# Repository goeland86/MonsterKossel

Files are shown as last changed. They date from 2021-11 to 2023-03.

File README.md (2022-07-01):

# Monster Kossel: v3.0

A Kossel-inspired Delta printer with:
* large build volume
* an incredibly stiff frame
* an easily fully enclosed build volume
* piezo-based bed probing (Andromeda layout from precisionpiezo.co.uk)
* easy to tune / upgrade setups
* M3 and M5 screws only

The image is missing the second rod per tower, and is not showing some of the screws - this is normal. A photo of the final, assembled printer is coming.
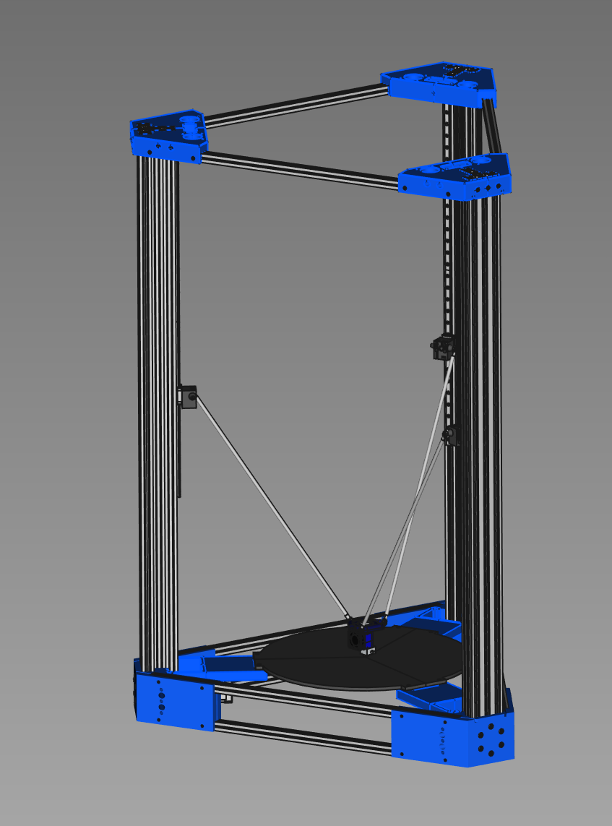
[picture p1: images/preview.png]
Monster Kossel


## Design history:

V1 started with my taking a Kossel XL idea but noticing the OpenBeam frames just weren't rigid enough. 
I tweaked the STL files with Blender to use 2040 towers instead. It was better... But still a bit wobbly.

V2 was still done with Blender but introduced the T-based towers using 2060 and 2040 extrusions for the maximum possible rigidity.
It also introduced the concept of the fully enclosed build volume. 

It became the test bed for a series of remote drive extruder designs by Dan Cook, which are proving to be incredibly reliable.
The latest iteration of which is a mix of extruder and effector design for Kossel sized rod widths. 
It's proven to handle flexibles as good as a Prusa MK3's stock extruder, if not better.

V3, shared here, is an ongoing effort to properly draw and design a revision of V2 in a proper CAD format.
The aim is to further enhance the experience by incorporating many lessons learned with regards to cable management.
It is currently being drawn and assembled in FreeCAD 0.19_pre release, using the Assembly4 plugin.

## Assembly file(s)

The main assembly file is `MonsterKossel_assembly.FCStd`, made for the `Assembly3` workbench that you can find from the addon manager, use with FreeCAD 0.20+.

The other workbench that is required is the `Fasteners` workbench, to include all the screws & nuts into the assembly.

## Current development status

The main frame of V3 has not yet been fully tested in real life, and the CAD design is undergoing multiple improvements as the tests continue. However at this stage the mechanics are considered solid and the dimensions will not change significantly.
Any further improvements will be to improve assembly, printability or esthetics.

Dan Cook has released his all in one effector / direct drive extruder on [Thingiverse](https://www.thingiverse.com/thing:4886240/files), including the telescoping shaft of my conception.

Carriages have been redrawn as the original Kossel carriages designed for the MGN19H carriage pattern don't have enough rigidity when using an adapter plate.

All parts will are printed in PETG rather than PLA for heat resistance. ABS, PCTG, PC are all possible options for the printed parts to be used. Avoid Nylons and other more flexible materials, as the parts need to be as rigid as possible to maintain dimensional stability of the assembled printer.

The top cover will come in two versions: one as a blank template for builders to customize the layout of elements on their own, the other as I intend to build it, using 100mm (a little under 4" diameter, standard in Europe) AC extraction ventilation systems with filters, wiring and filament paths etc.

### BOM

#### Printed parts:

Best rigidity achieved using PETG or similar flexibility of material, with 1 or 1.2mm thick walls, and 20% infill, and 0.2 or 0.3 layer height. Avoid PLA at least for the motor frames to avoid heat-induced deformation over time.

- bottom corner: 3x

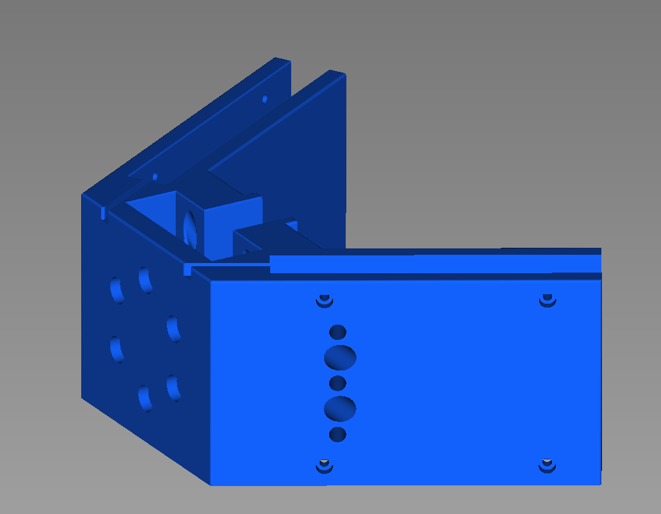
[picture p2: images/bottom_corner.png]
Bottom corner


- motor frame: 3x (print upside down, flip 180 degrees along x or y in your slicer)

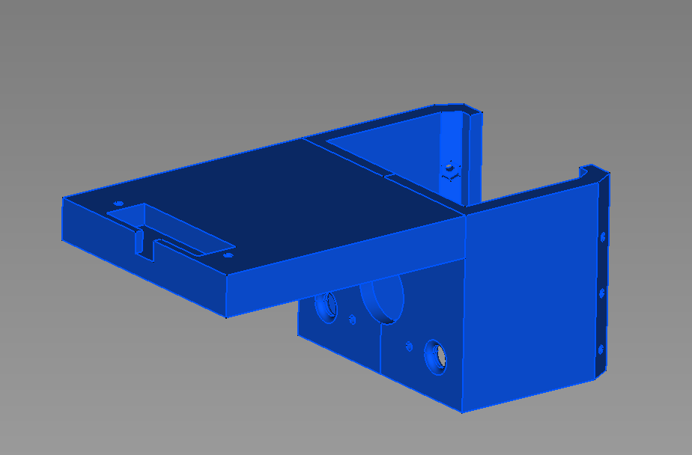
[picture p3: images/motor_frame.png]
Motor frame


- top corner: 3x

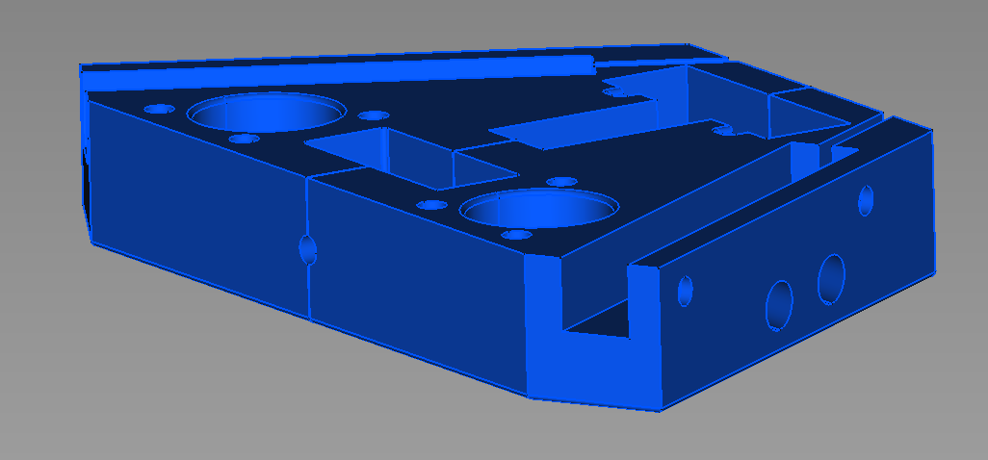
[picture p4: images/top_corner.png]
Top corner


- carriage belt tensioner: 3x

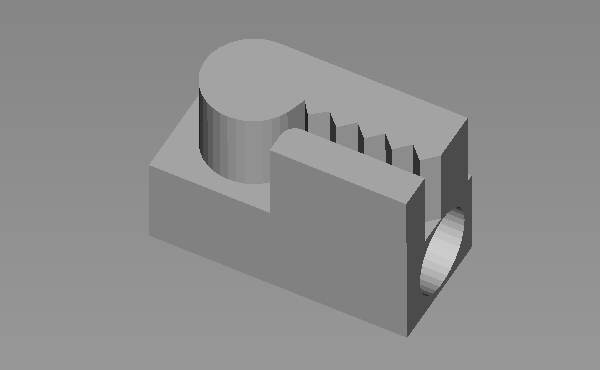
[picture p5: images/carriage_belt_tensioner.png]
carriage belt tensioner


- mgn9c carriage: 3x

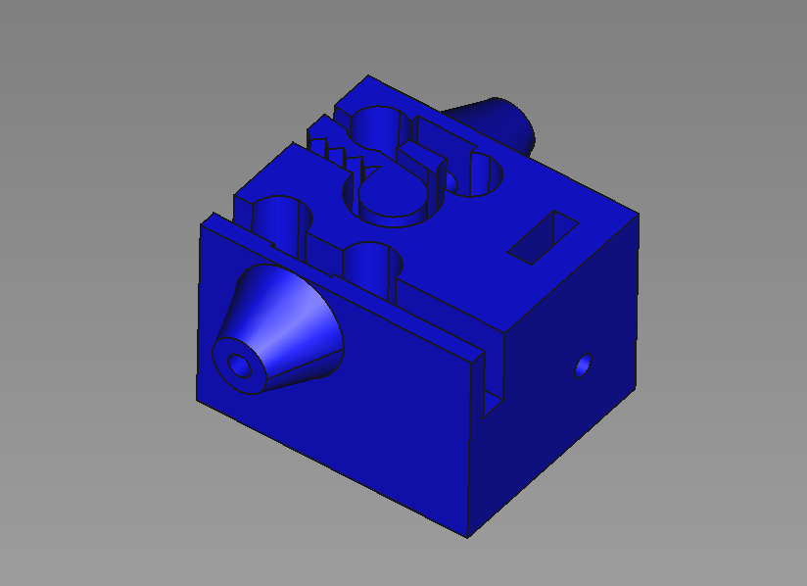
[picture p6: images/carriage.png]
carriage


- extruder parts (all are x1, printed with finer layer height is better):
  - 18T bevel
  - 6T bevel
  - Body top
  - Delta effector
  - Latch
  - Main body center
  - Main body left
  - Main body right

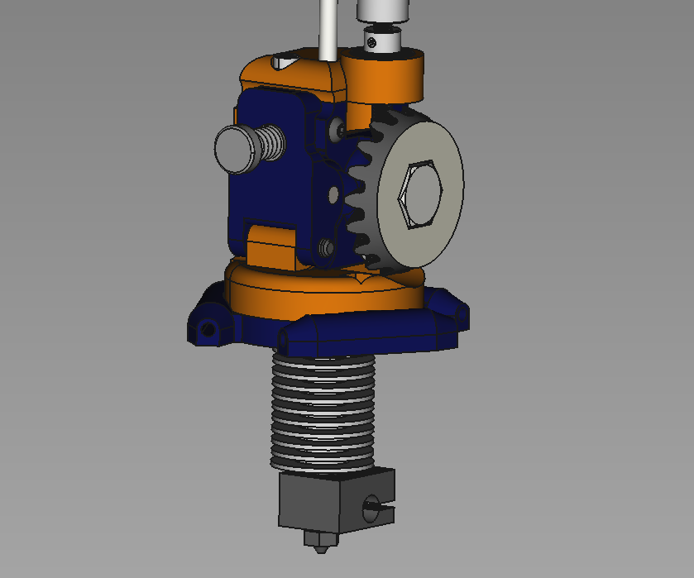
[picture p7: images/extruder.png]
extruder


OPTIONAL 

- base corner holder 6x (recommend in flexible material to dampen vibrations, to hold the printer properly in place on a plate/table).

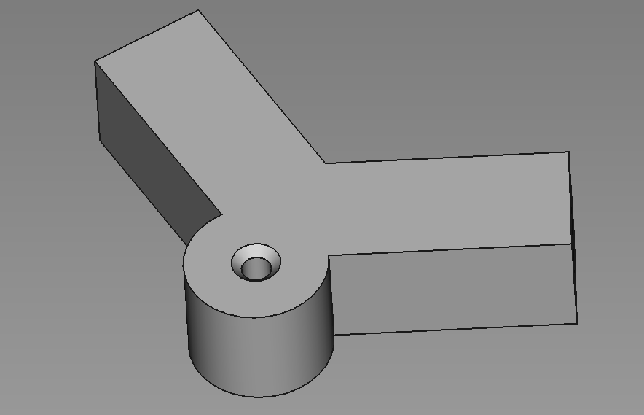
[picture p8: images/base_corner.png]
base corner


- CPAP-fan-diffuser 1x (to bring in part cooling air from an outside fan blowing cold air onto the part, recommend PETG/high temp material)

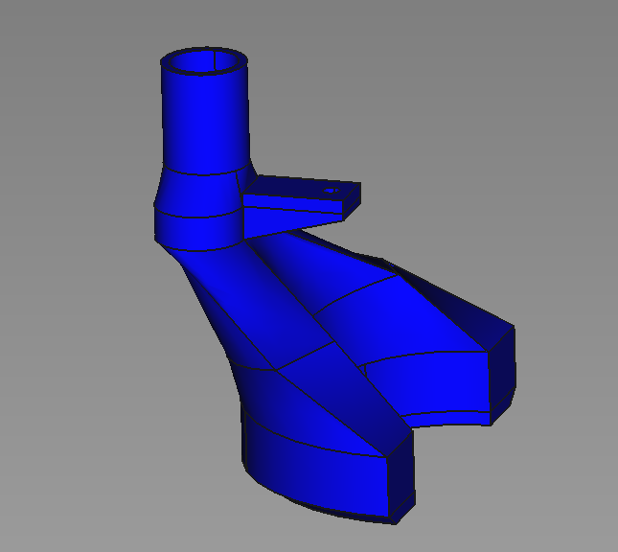
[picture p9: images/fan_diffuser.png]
fan diffuser


If using an E3D watercooling kit for the hotend:

- Watercooling-pump-bracket-bottom x1

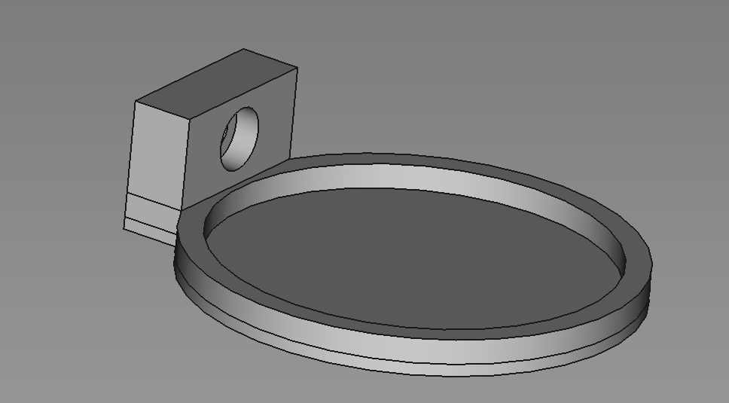
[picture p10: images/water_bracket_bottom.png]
watercooling bracket bottom


- Watercooling-pump-bracket-top x1

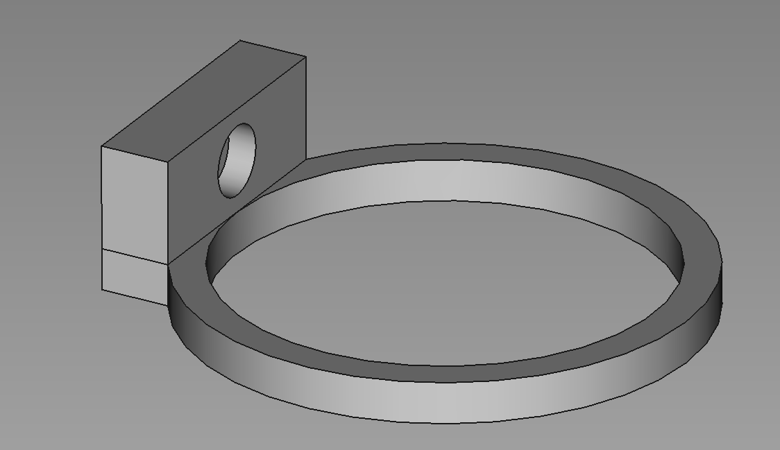
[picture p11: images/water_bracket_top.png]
watercooling bracket top


- bearing ujoint cube x2

- bearing ujoint fitting x4

#### Non-printed parts:

- Power supply (count about 40 to 50W for the motors, plus what your hotend, electronics and fans use)
- Electronics controller (32bit controller highly recommended, numerical precision requires extra computational power). I run mine with a [Recore](https://www.iagent.no/product/recore/)
- MGN9H rails: 3
- MGN9C carriages: 3
- NEMA17 motors: 4
- Traxxas 5347 spherical joints: 12
- carbon / aluminum rods: estimate 6x 390mm for a 350mm bed - identical lengths required (< 0.1mm difference in lengths recommended)
- E3D V6 hotend with M-12 threaded heatsink ([blue heatsink](https://e3d-online.com/products/v6-threaded-heatsink)): 1 (if enclosed, consider getting a [water-cooled, M12-mounting](https://www.thingiverse.com/thing:3088118/files) heatsink or hotend instead)
- Telescoping torque shaft:
 - aluminum square tubing 9mm on the side : length to be measured
 - aluminum square tubing 12mm on the side : length to be measured
 - aluminum square tubing 15mm on the side : length to be measured
 - double u-joints with 4mm shaft: 2
 - round 4mm steel rod: 2x 50mm
- [PrecisionPiezo Andromeda](https://www.precisionpiezo.co.uk/product-page/andromeda) : 3
- [PrecisionPiezo Universal Piezo Z-Probe PCB](https://www.precisionpiezo.co.uk/product-page/universal-piezo-z-probe-pcb-v2-x-for-1-2-3-or-more-piezos) : 1
- Endstops: 3 (optional if your electronics & firmware supports high precision sensorless homing)
- Electrical wiring (red and black recommended in equal lengths): ~ 10m of each color recommended. Lots of variability depending on placements.
- GT2-6mm wide belt: 3 times twice the vertical extrusion length (for 1m tall, get 3 of 2m length, will give ~100mm of slack per tower)
- Control board: minimum of 4 stepper drivers + 2 heater controls (2 temperature inputs, 2 MOSFETs)
- PSU: Minimum of 650W if heatbed is not using AC and a relay
- M3 nuts: 69 (bottom assembly: 42, top frame: 12, motor frames: 9, idler centering: 6)
- M3 washers: 18 (motor frames: 18)
- socket cap M3x5: 15 (motor frames: 3, carriage assemblies: 12)
- socket cap M3x8: 69 (tower assemblies: 45, top frame: 12, motor frames: 12)
- socket cap M3x10: 24 (bottom frame: 24)
- button cap M3x15 : 6 (motor frames: 6) - can also be longer, for bed assembly, but no longer than M3x30 (blocked by the NEMA 17 motor otherwise)
- socket cap M3x16: 18 (bottom frame assembly: 18) - can also be M3x15
- countersunk head M3x20: 6 (bottom frame assembly: 6)
- socket cap M3x30: 3
- socket cap M5x8: 24 (top frame: 12, bottom frame: 12)
- socket cap M5x10: 9 (top frame: 9)
- socket cap M5x12: 18 (bottom frame: 18)
- socket cap M5 Openbuilds flat nuts: 51
- F623ZZ flanged bearings: 6 OR idler pulleys for GT2x6mm : 3
- Nema 17 motors (1.8 degree is fine, 1.2-1.5A capability sufficient): 4
- 16-teeth pulley for 5mm shaft (with M3x4 set screw): 3
- Acrylic/glass/wood sheet (3mm): 3x 810mm x 500mm (use dimensions of side_panel file instead)
- Acrylic/wood/carbon/fiberglass sheet (5mm): 450mm x 400mm (cut using top_cover dimensions)
- Extruder parts:
  - M8x35 bolt: 1
  - MR 148ZZ bearings (8mm ID, 14mm OD, 4mm thick): 4
  - Bondtech [dual drive gears 1.75 / 8](https://www.bondtech.se/product/drivegear-kits/): 1 set
  - M3x12 hex socket cap
  - M4x40 set screw
  - M3x8 hex socket cap
- MR 84 ZZ bearings (ID 4mm, OD 8 mm, 3mm thick) x4
- Needle bearings (ID 4mm, OD 7mm, length 7mm) x4

##### Optional parts

- [CPAP fan + driver](https://www.aliexpress.com/item/33041228096.html?spm=a2g0o.9042311.0.0.38a54c4dUW6Yg9)
- CPAP mounting plate printed 1x
- [E3D watercooling kit](https://e3d-online.com/products/water-cooling-kit)
- Printed M12 nut 1x (make it 100% infill for robustness)

## Credit

I want to thank [Dan Cook](https://www.thingiverse.com/dancook3d/designs) for his wonderful [bevel geared extruder design](https://www.thingiverse.com/thing:4886240/files). We've exchanged a fair bit to iterate the design before he published it, and I'm happy to see that project being this successful on its own.

Additionally he made a [great delta carriage](https://www.thingiverse.com/thing:3070352) which I'm using the tensioner design from in this project.
Both of those designs you'll find the relevant step files in the `STEP` subfolder, and they're straight copies from his Thingiverse designs. I just included them for completeness here.

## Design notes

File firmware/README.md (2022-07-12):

### Monster Kossel: the firmware

At time of writing, the Monster Kossel has never been run with Marlin.

There's no reason it can't. A good SKR board and some finagling with Marlin will get you there for sure.

However I have been a long-time fan and contributor to the [Intelligent-Agent](https://github.com/intelligent-agent/) series of boards for the firmware.

Versions 1 and 2 of the Monster Kossel have run on the original Replicape + Beaglebone Black combo. Then when it was made available to me for beta testing, I switched it over to a Recore.
This means that I've only run two firmwares on this delta: Redeem (abandoned firmware for the Replicape), and Klipper.

Because I have never tried (nor wanted to) run it on any other board, I can only provide my Klipper configuration file for Recore for my delta.

# WARNING!

If you do not use Recore, the klipper config may be deprecated. That is because Recore is currently running its own fork of Klipper.
While it was developed specifically for Klipper usage, some new chip supports were needed in the base code, and as far as I know this hasn't yet merged upstream.

If you're using Recore and are building a 350mm bed, with 1000mm tall extrusions, this should be nearly plug & play. Simply make sure to re-measure your delta rod lengths and re-run the calibration routine.

Obviously if you're diverging from the BOM listed for the design, you'll need to adjust the config accordingly.

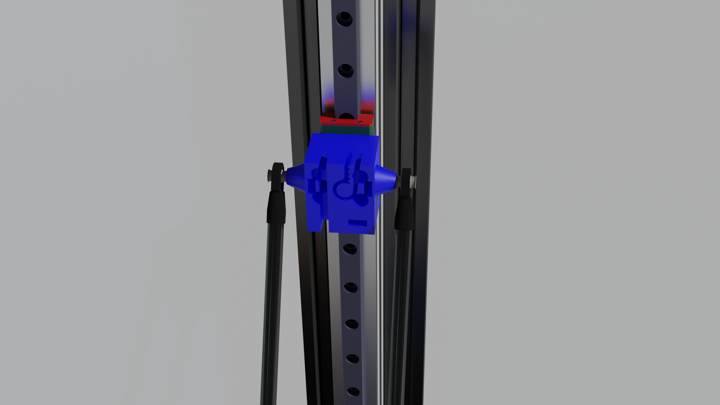
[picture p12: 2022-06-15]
images/carriage_detail.png

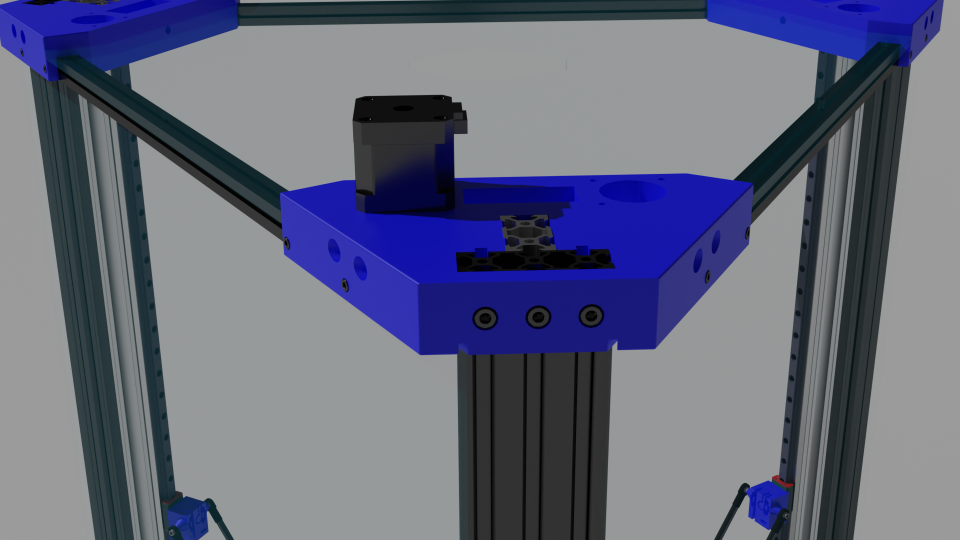
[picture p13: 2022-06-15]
images/Top_corner_motor_zoom.png

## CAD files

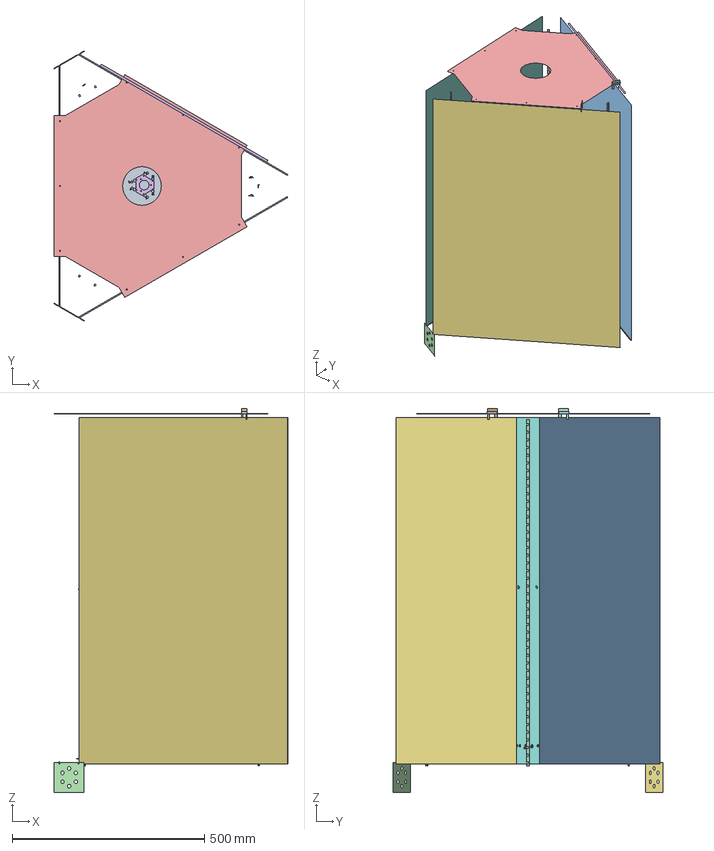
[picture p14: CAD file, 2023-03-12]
Assembly.FCStd
608.1 x 701.3 x 998.5 mm
_Element
_Element001
_Element002
_Element003
_Element004
_Element005
_Element006
_Element007
_Element008
_Element009
_Element010
_Element011
_Element012
_Element013
_Element014
_Element015
_Element016
_Element017
_Element018
_Element019
_Element020
_Element021
_Element022
_Element023
_Element024
_Element025
_Element026
_Element027
_Element028
_Element029
_Element030
_Element031
_Element032
_Element033
_Element034
_Element035
_Element036
_Element037
_Element038
_Element039
_Element040
_Element041
_Element042
_Element043
_Element044
_Element045
_Element046
_Element047
_Element048
_Element049
_Element052
_Element053
_Element054
_Element055
_Element057
_Element058
_Element059
_Element060
_Element061
_Element063

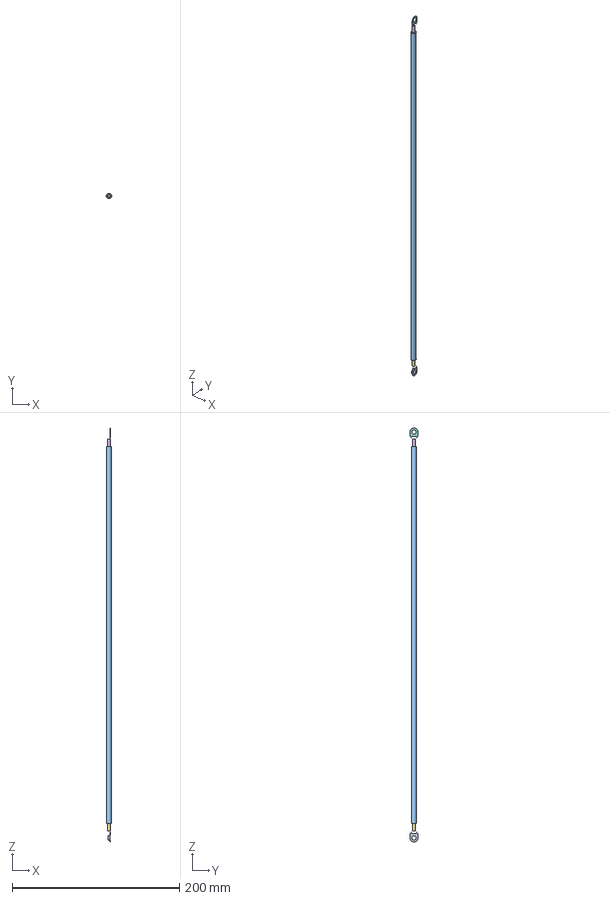
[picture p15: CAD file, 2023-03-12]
rod_assembly.FCStd
6.60 x 9.70 x 494.4 mm
Element
_Element
_Element002
_Element004
_Element006
_Element007
_Element008
_Element009
_Element010
_Element011
_Element012

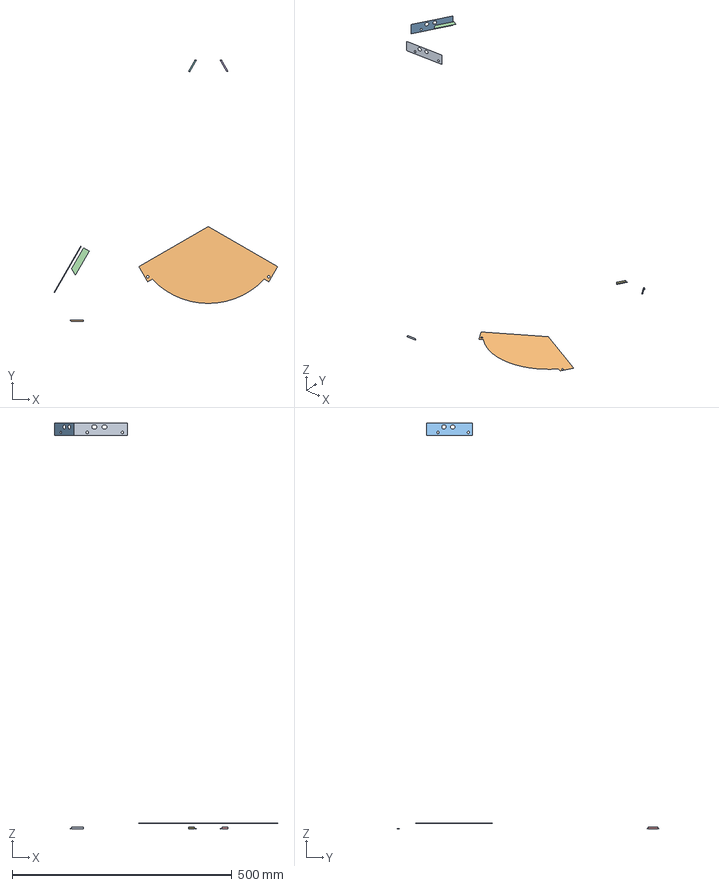
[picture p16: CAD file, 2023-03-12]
Complete_printer.FCStd
508.2 x 607.0 x 923.9 mm
_Element001
_Element002
_Element004
_Element006
_Element008
_Element010
_Element014
_Element016
_Element020
_Element022

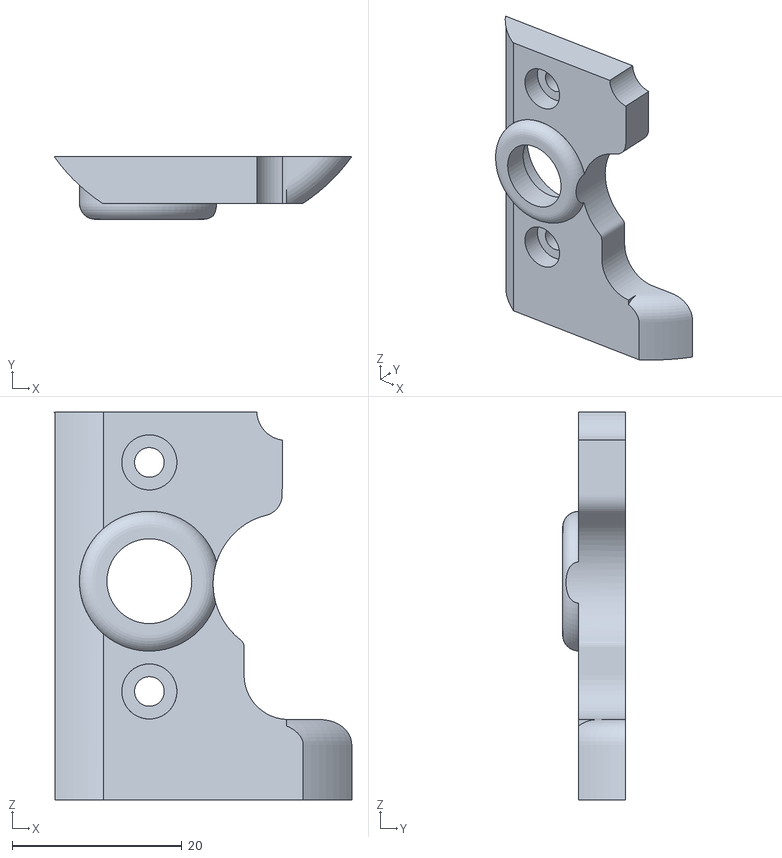
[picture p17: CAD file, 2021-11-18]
STL/effector-extruder-files/Main_Body_Right.stl
35.1 x 7.40 x 45.7

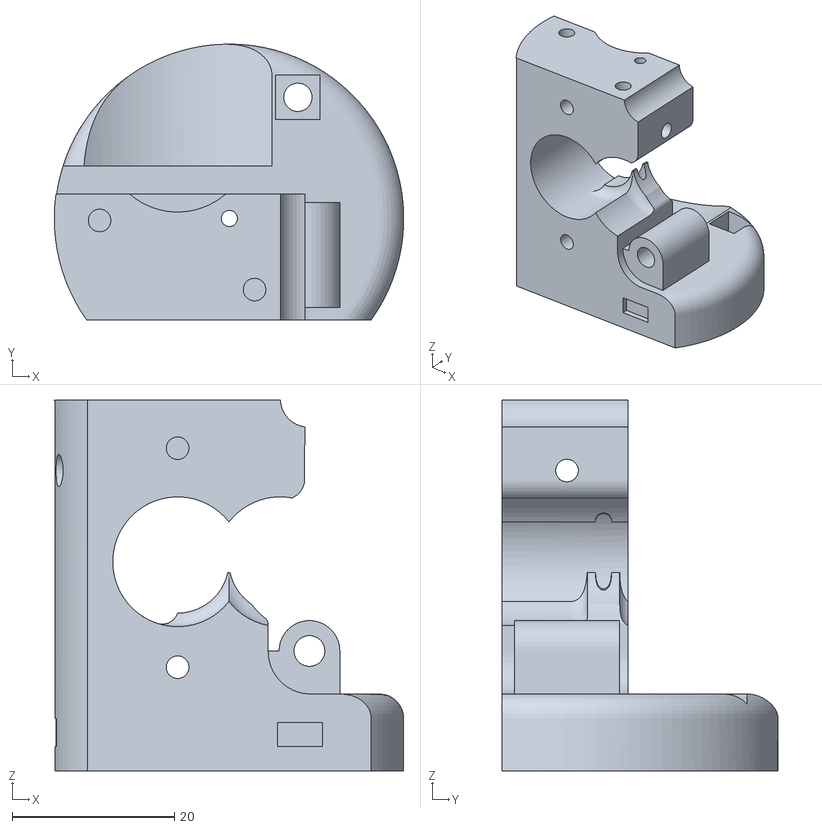
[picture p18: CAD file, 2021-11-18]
STL/effector-extruder-files/Main_Body_Center.stl
43.1 x 34.0 x 45.7

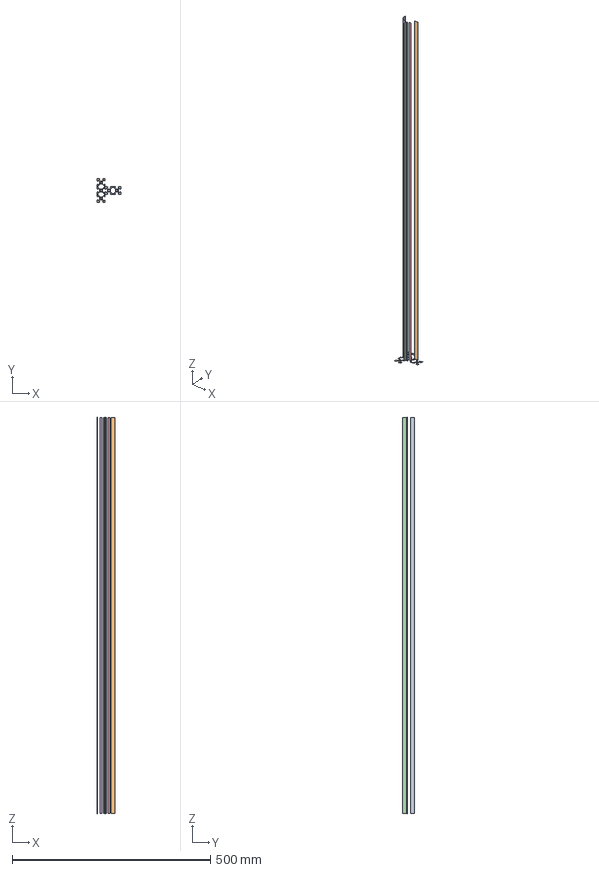
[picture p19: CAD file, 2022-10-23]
Vertical_extrusion_assembly.FCStd
60.0 x 60.0 x 1000.0 mm
Element
Element001
_Element
_Element001
_Element002
_Element003
_Element004
_Element005
_Element006
_Element007

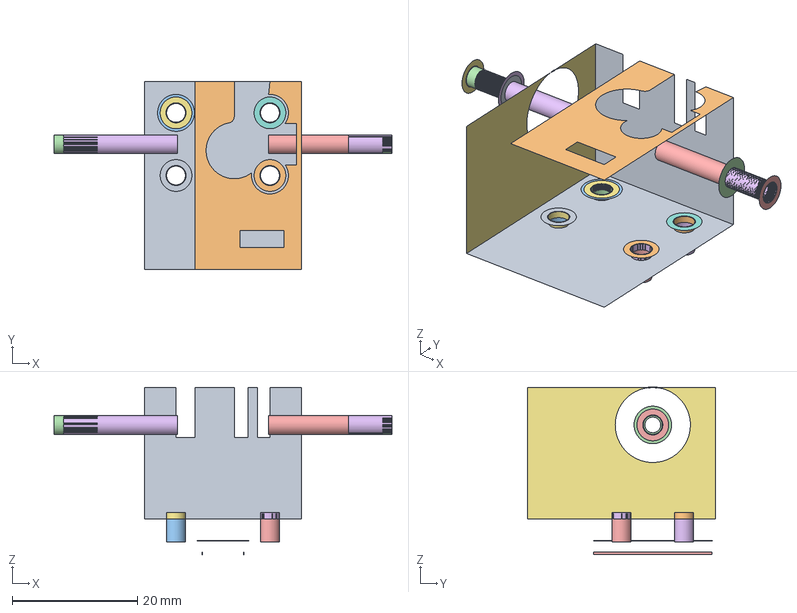
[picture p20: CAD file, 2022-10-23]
carriage_assembly.FCStd
54.0 x 30.0 x 26.7 mm
Element
Element001
Element002
Element003
Element004
Element005
Element006
Element007
Element012
_Element
_Element008
_Element010
_Element011
_Element012
_Element015
_Element016
_Element017
_Element018
_Element019
_Element020
_Element021
_Element022
_Element023
_Element024
_Element025
_Element026
_Element027
_Element032
_Element033
_Element035
_Element036
_Element037
_Element038
_Element039
_Element040
_Element041
_Element042
_Element043

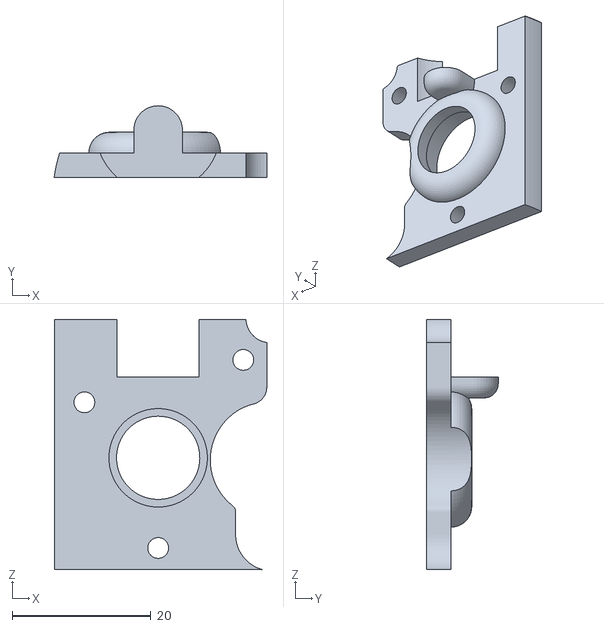
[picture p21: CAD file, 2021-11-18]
STL/effector-extruder-files/Main_Body_Left.stl
30.7 x 10.3 x 36.0

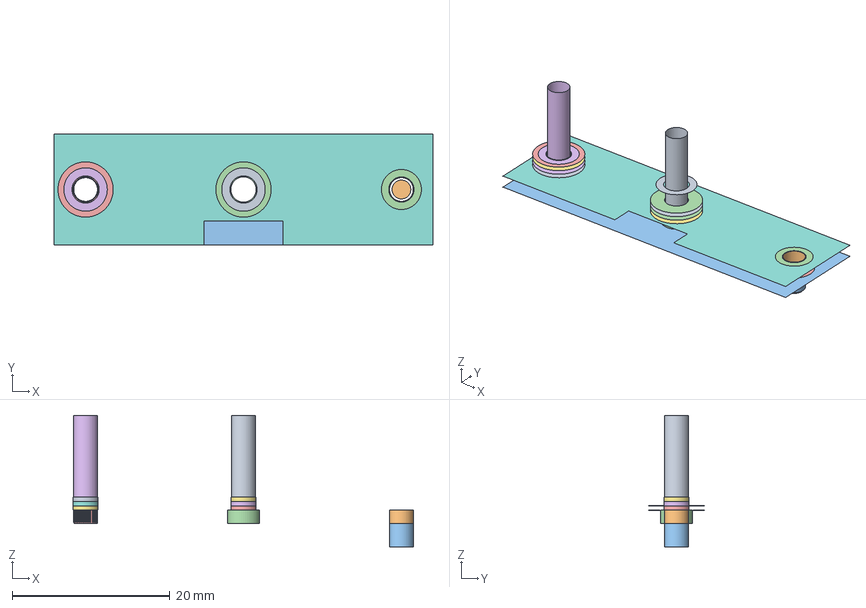
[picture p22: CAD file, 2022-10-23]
piezo_assembly.FCStd
48.0 x 14.0 x 17.0 mm
Element
Element002
_Element
_Element001
_Element002
_Element003
_Element004
_Element005
_Element006
_Element007
_Element008
_Element009
_Element010
_Element011
_Element012
_Element013
_Element014
_Element015
_Element016
_Element017
_Element018
_Element019
_Element020
_Element021
_Element022
_Element023
_Element024
_Element025
_Element026
_Element027
_Element028
_Element029
_Element030
_Element031
_Element032
_Element033
_Element034

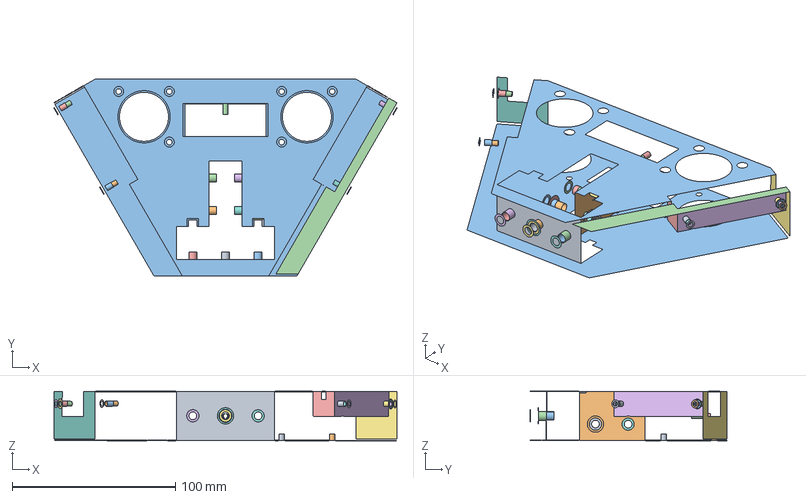
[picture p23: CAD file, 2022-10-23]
top_corner_assembly.FCStd
210.1 x 120.5 x 30.3 mm
Element
Element001
Element002
Element003
Element004
Element005
Element006
Element007
Element008
Element009
_Element
_Element001
_Element002
_Element003
_Element004
_Element005
_Element006
_Element007
_Element008
_Element009
_Element010
_Element011
_Element012
_Element013
_Element014
_Element015
_Element016
_Element017
_Element018
_Element019
_Element020
_Element021
_Element022
_Element023
_Element024
_Element025
_Element026
_Element027
_Element028
_Element029
_Element030
_Element031
_Element032
_Element033
_Element034
_Element035
_Element037
_Element038
_Element039
_Element041
_Element042
_Element043
_Element045

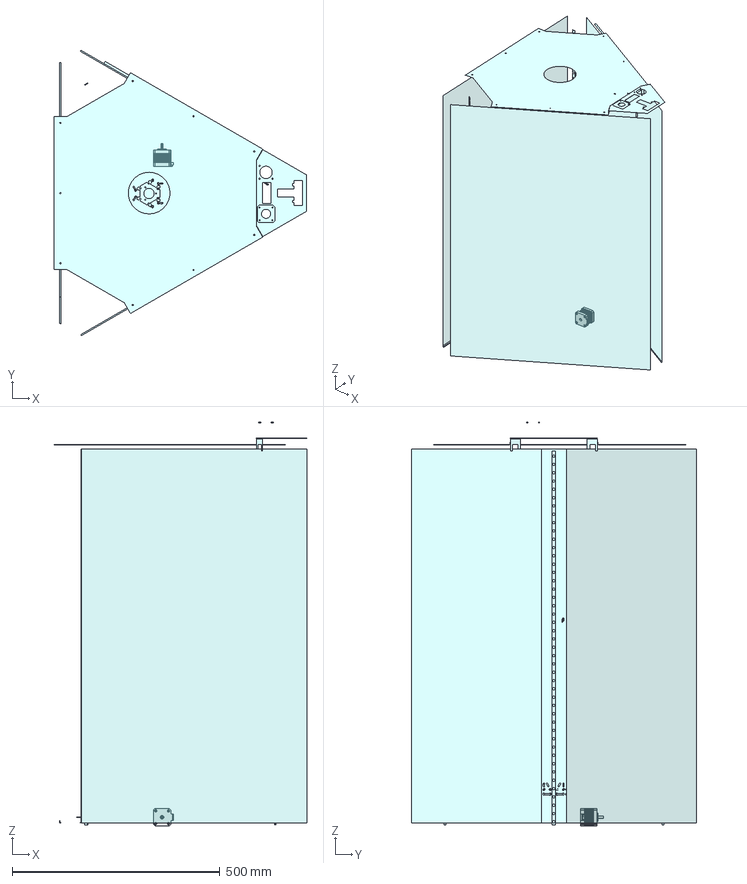
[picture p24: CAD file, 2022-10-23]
Assembly-for-render.FCStd
607.9 x 686.7 x 972.0 mm
_Element
_Element001
_Element002
_Element003
_Element004
_Element005
_Element006
_Element007
_Element008
_Element009
_Element010
_Element011
_Element012
_Element037
_Element038
_Element040
_Element041
_Element042
_Element043
_Element044
_Element045
_Element046
_Element048
_Element052
_Element054
_Element058
_Element059
_Element060
_Element061
_Element081
_Element085
_Element086
_Element088
_Element092
_Element095
_Element098
_Element100
_Element110
_Element112
_Element114
_Element115
_Element123
_Element124
_Element125
_Element126
_Element127
_Element128
_Element129
_Element130
_Element131
_Element132
_Element133
_Element134

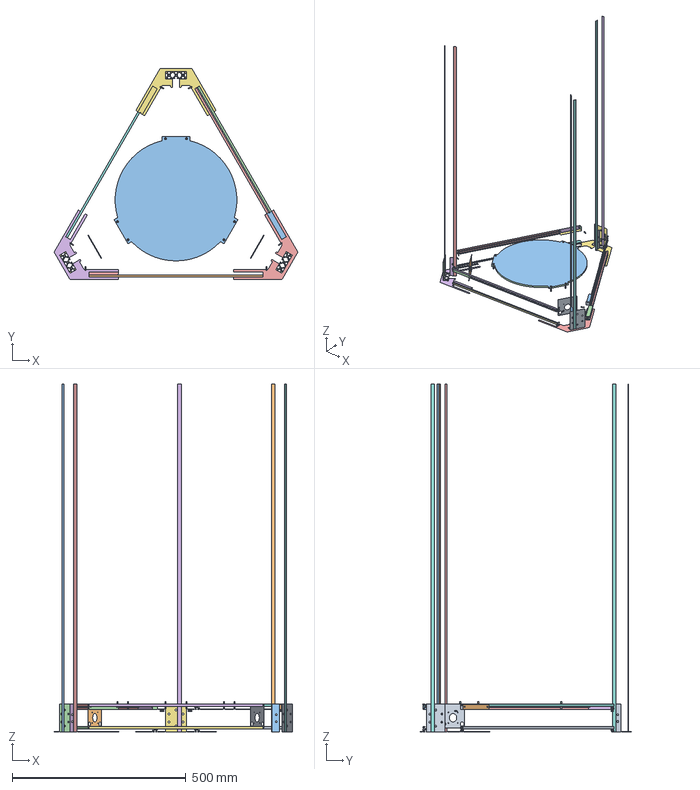
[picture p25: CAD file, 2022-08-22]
bottom_frame_assembly.FCStd
700.5 x 606.8 x 1000.0 mm
Element019
Element020
_Element
_Element001
_Element002
_Element003
_Element004
_Element005
_Element006
_Element007
_Element008
_Element009
_Element010
_Element011
_Element012
_Element013
_Element014
_Element015
_Element016
_Element018
_Element019
_Element020
_Element021
_Element022
_Element023
_Element024
_Element025
_Element026
_Element042
_Element044
_Element046
_Element047
_Element048
_Element050
_Element051
_Element053
_Element055
_Element057
_Element058
_Element060
_Element061
_Element063
_Element065
_Element067
_Element068
_Element070
_Element071
_Element073
_Element075
_Element076
_Element077
_Element078
_Element079
_Element080
_Element081
_Element082
_Element083
_Element084
_Element085
_Element086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

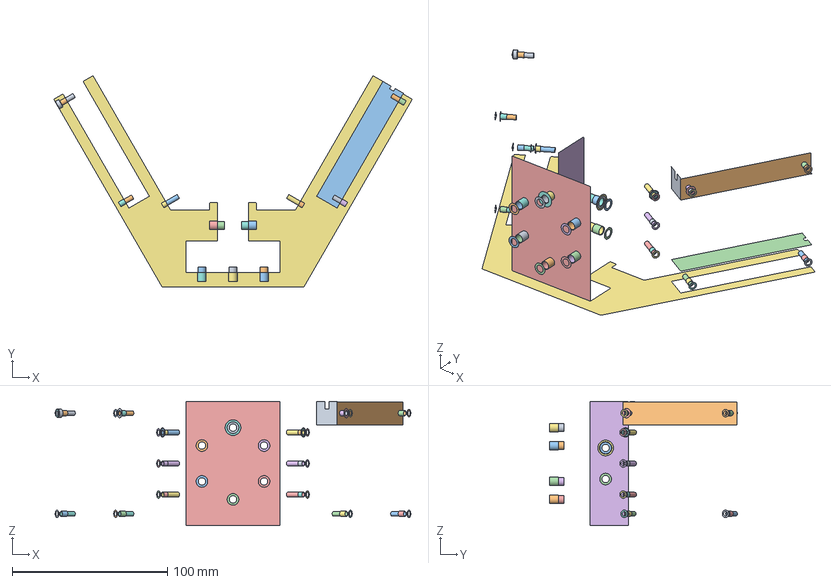
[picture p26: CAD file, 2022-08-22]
bottomCorner_assembly.FCStd
230.4 x 137.5 x 80.0 mm
Element
Element001
Element002
Element003
Element004
Element005
_Element
_Element001
_Element003
_Element005
_Element007
_Element009
_Element011
_Element013
_Element015
_Element017
_Element019
_Element021
_Element023
_Element025
_Element027
_Element029
_Element031
_Element033
_Element035
_Element037
_Element039
_Element041
_Element043
_Element045
_Element047
_Element049
_Element050
_Element051
_Element052
_Element053
_Element054
_Element055
_Element056
_Element057
_Element058
_Element059
_Element060
_Element061
_Element062
_Element063
_Element064
_Element065
_Element066
_Element067
_Element068
_Element069
_Element070
_Element071
_Element072
_Element075
_Element077
_Element081
_Element083
_Element086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

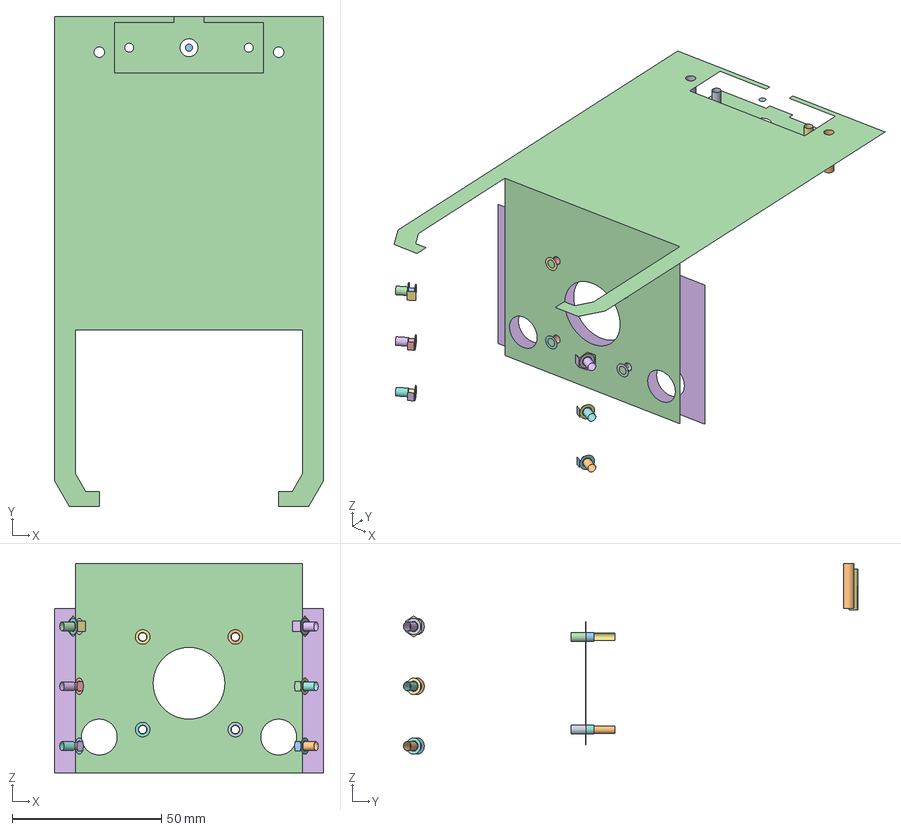
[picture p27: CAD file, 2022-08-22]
motor_frame_assembly.FCStd
90.0 x 164.1 x 71.6 mm
Element
Element001
Element002
_Element
_Element001
_Element002
_Element003
_Element004
_Element005
_Element006
_Element007
_Element008
_Element009
_Element010
_Element011
_Element012
_Element013
_Element014
_Element015
_Element016
_Element017
_Element018
_Element019
_Element020
_Element021
_Element022
_Element023
_Element024
_Element025
_Element026
_Element027
_Element028
_Element029
_Element030
_Element031
_Element032
_Element033
_Element034
_Element035
_Element036
_Element037
_Element038
_Element039
_Element040
_Element041
_Element042
_Element043
_Element044
_Element045
_Element046
_Element047
_Element048
_Element049
_Element050
_Element051
_Element052
_Element053

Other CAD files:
2D drawings/Bed-350mm-diameter.dxf
Optional/CPAP_quiet_case.FCStd
STEP/Optional/Watercooling-pump-bracket-bottom.step
STEP/Recore_mount-80mm_fan_mount.step
Base_corner_holder.FCStd
Bed.FCStd
MGN9C.FCStd
MGN9CZFC-HiwinCorporation-3D-10-31-2021.FCStd
MGNR9R900CM-HiwinCorporation-3D-10-31-2021.FCStd
MonsterKossel_chassis.FCStd
MonsterKossel_dimensions.FCStd
Nema17WithPulley.FCStd
OpenBeam1515.FCStd
OpenBuilds2040.FCStd
OpenBuilds2060.FCStd
Optional/CPAP-fan-driver-mounting-plate.FCStd
Optional/CPAP-fan-mounting-plate.FCStd
Optional/M12_printable_nut.FCStd
Optional/Watercooling-pump-bracket-bottom.FCStd
Optional/Watercooling-pump-bracket-top.FCStd
PrecisionPiezoAndromeda.FCStd
Rail.FCStd
STEP/Base_corner_holder.step
STEP/Bed-6mm.step
STEP/Bed.step
STEP/Bondetech mini gears.step
STEP/F623ZZ v2.step
STEP/Insulation_layer.step
STEP/MGN9CZFC-HiwinCorporation-3D-10-31-2021.stp
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

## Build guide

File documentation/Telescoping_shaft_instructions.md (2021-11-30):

# Telescoping torque shaft

The concept of a delta printer is to keep the effector as light as possible to avoid having too much mass and inertia at the print head. However extrusion of filament based systems is proven to be more efficient for multiple parameters when the drive of the filament is closer to the hotend - generally referred to as direct-drive systems.

Mechanically, there is no obligation to have the motor and the filament drive gears in the same location. It is done out of convenience and simplicity, but at the cost of weight. Even a pancake NEMA17 will weight a significant amount.

By keeping the drive gear on the effector but moving the motor off of it, we retain the main advantage of the delta printer of a light effector, but we also keep the filament drive near the hotend. I dub this concept (not entirely accurately): remote direct drive extrusion.

The key for a delta effector to do this effectively is to have a torque transmission that is as slop-free as possible, yet allows for a full range of motion of the effector. The telescoping torque shaft is my approach to doing so.

## Limitations

The shaft will need to use a double-u joint on each end, and telescope a significant amount. For the Monster Kossel project, I've had to do a triple-joint telescoping shaft to get the minimum length (when the hotend is at its home position - top of the print volume), and reach every part of the build plate (full extension). The length differential was close to a factor of 2.8 or 2.9. Depending on how tall you build the printer, that factor may change significantly. If it reaches above 3, you will need a 4-part telescoping shaft. If it drops to slightly less than 2, you can do it as a 2-part shaft.

Also my local experiments have shown that it works best if the driving motor shaft is placed such as to minimize the maximum angle that is required for printing. That is generally reached when the effector is at max printable height on the farthest side of where the motor is mounted. Thus, mounting the motor in the center would be most effective. However, I intend on having an air filter assembly in the center of the top frame. So mounting it in the middle of one of the top extrusions is the next best option.

The double-u joints will bring on a noticeable increase in effort for rotation above 30 degrees of axle transmission.

## Measuring the dimensions

The way the telescoping shaft works is by looking at what the minimum and maximum lengths should be across the print volume range of motion.

As indicated in the limitations section, the maximum extension is when the print head is at the opposite end of the horizontal, and at the build plate. Call this ***Lmax***.

The minimum extension will be at the upper-most printing height underneath the motor mount. This will be ***Lmin***.

If 3x ***Lmin*** > ***Lmax*** > 2 x ***Lmin***, then you will need a 3-segment telescoping. Keep in mind that there will be a minimum fixed distance added by each segment.

Consider the case where ***Lmin*** is 450mm and ***Lmax*** is 950mm. In that case your segment's maximum length is not going to be 450mm. Instead if will be closer to 430 or even 420mm length, because of the 4mm steel pins onto which the double-u joints attach on either end of the shaft.

The maximum extension, then, is not 430mm x 3 = 1290mm. The segments need to keep between 30 and 40mm of overlap, to transmit torque and keep proper alignment. So the calculation then returns: 3x (430-40) = 3x 390 = 1170mm. Still plenty given the distance of 950mm required.

## Assembly considerations

My prototype shaft uses 3 square aluminum tubing segments of nearly matching inner and outer sizes. The 7.5mm external tubing fits with about 0.5mm of tolerance in the 11.5mm external tubing (wall thickness is 1.5mm). I glued small felt pads on the ends of the rear of the 7mm segment, and the inside front of the 11.5mm segment. They are super-glued in place. To further smooth the motion, I added some PTFE grease. The 11mm segment also has felt pads super-glued to the rear of its segment. It then fits inside a 15.5mm segment where the front has pads on the inside, and the back is drilled for an M3x20 screw to go through and lock the printed cap in which the 4mm dowel attaches.

The 0.5mm gap is frustratingly small for the felt pads, as the thinnest I could find was closer to 1mm. However it compresses nicely and the PTFE grease lets it slide in without too much hassle or damage.

To guarantee proper telescoping operations, as well as avoiding getting grease on the filament's PTFE tube, I recommend attaching the outer-most segment to the effector, and the inner-most one to the motor. The reason for this is that gravity will be such that the inner-most tube will always extend fully first, before pulling the inner-most segment up. And conversely when it's being shrunk as the print head shrinks the distance, the first to start retracting will be pulled by gravity.

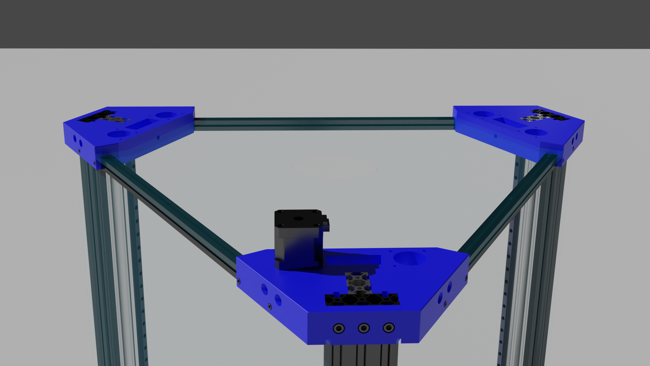
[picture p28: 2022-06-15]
images/Top_frame_assembly.png

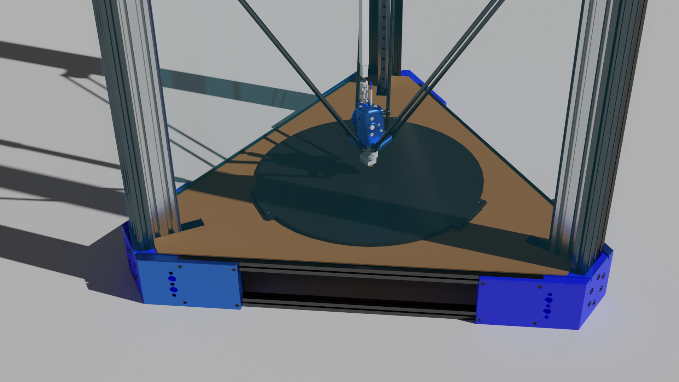
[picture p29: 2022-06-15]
images/Lower_frame_assembled.png

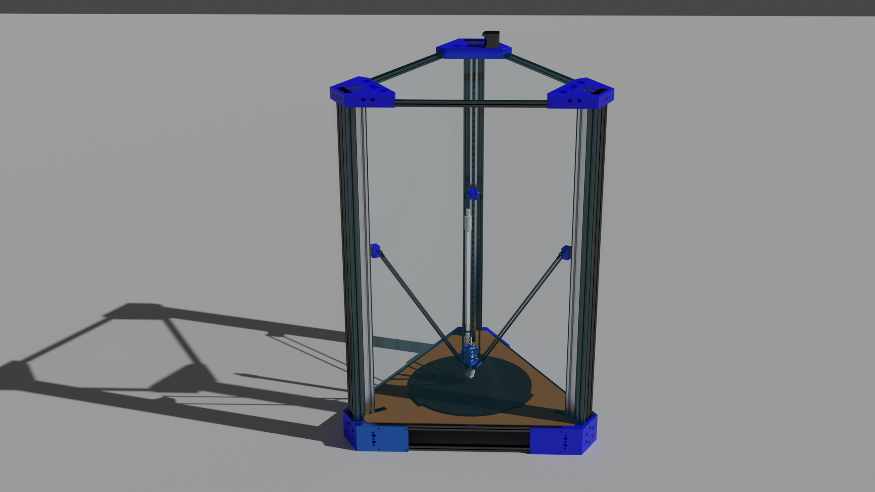
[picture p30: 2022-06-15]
images/whole_assembly_view.png

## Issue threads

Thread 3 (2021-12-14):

Minor problems during assembly.

goeland86, 2021-12-14:
- Lower triangle frame M3x10 screws are held too far back from the nut threads. Either needs M3x12 or a  pocket for the screw heads on the bottom corners.
- Holes for the M3x16 to hold bottom corners and motor frames together have too thin of a diameter to let the screw heads pass correctly. Increase diameter until the flats.
- Motor frame nuts holding to the bottom corner don't have enough space for being held while tightening. Add nut pockets.
- Adjust clearance between bed and triangular frame to account for silicone heater pad on the underside.

goeland86, 2021-12-15:
Still to be done: redefine the constraints in the various assemblies (motor_frame_assembly, bottom_assembly, assembly_a2plus) to account for the changes in part geometries.

Bonus points: redo the assembly using Linkstage3 (in a different branch) to see if it resolves the issues faced.

goeland86, 2022-02-11:
Closing as files are fixed and printer is assembled.

Closed 2022-02-11.

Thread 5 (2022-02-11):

Create fully parametric model

goeland86, 2022-02-11:
Build dimension calculations between files so that the relevant printer dimensions (extrusion lengths, rod lengths, belt lengths) can be derived from 2 inputs: build height & bed diameter.

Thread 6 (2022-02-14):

Use an alternate mounting point for the extruder motor.

goeland86, 2022-02-14:
Initially the design called for the extruder stepper to be held within the triangular frame at the top of the frame.

However this is proving impractical for several reasons:

- Clean cabling is a nightmare
- Angle of the double U joints at home position provides a rather sharp angle
- Stepper is held in the hottest part of the enclosure.

Instead, find a way to mount the stepper in a place where it will be better insulated from heat and have shallower angles for the double U-joints.

Closed 2022-03-06.

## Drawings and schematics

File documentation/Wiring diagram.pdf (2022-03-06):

## PSU 12V

220V

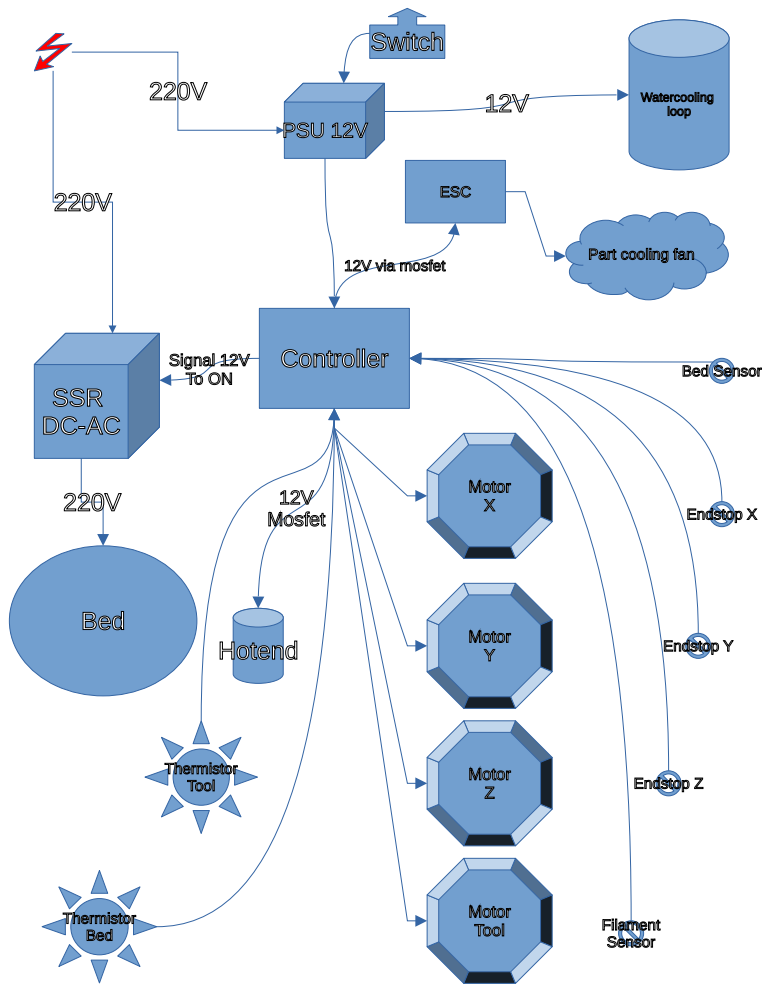
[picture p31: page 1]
Hotend; Watercooling loop; SSR DC-AC; Signal 12V; Controller; 12V Mosfet; Bed; Motor X; Endstop X; Endstop Z; Endstop Y Motor Y; Motor Z; Motor; Tool; Filament; Sensor; Bed Sensor; Thermistor Tool; Thermistor Bed; ESC; 12V via mosfet; Switch

Part cooling fan

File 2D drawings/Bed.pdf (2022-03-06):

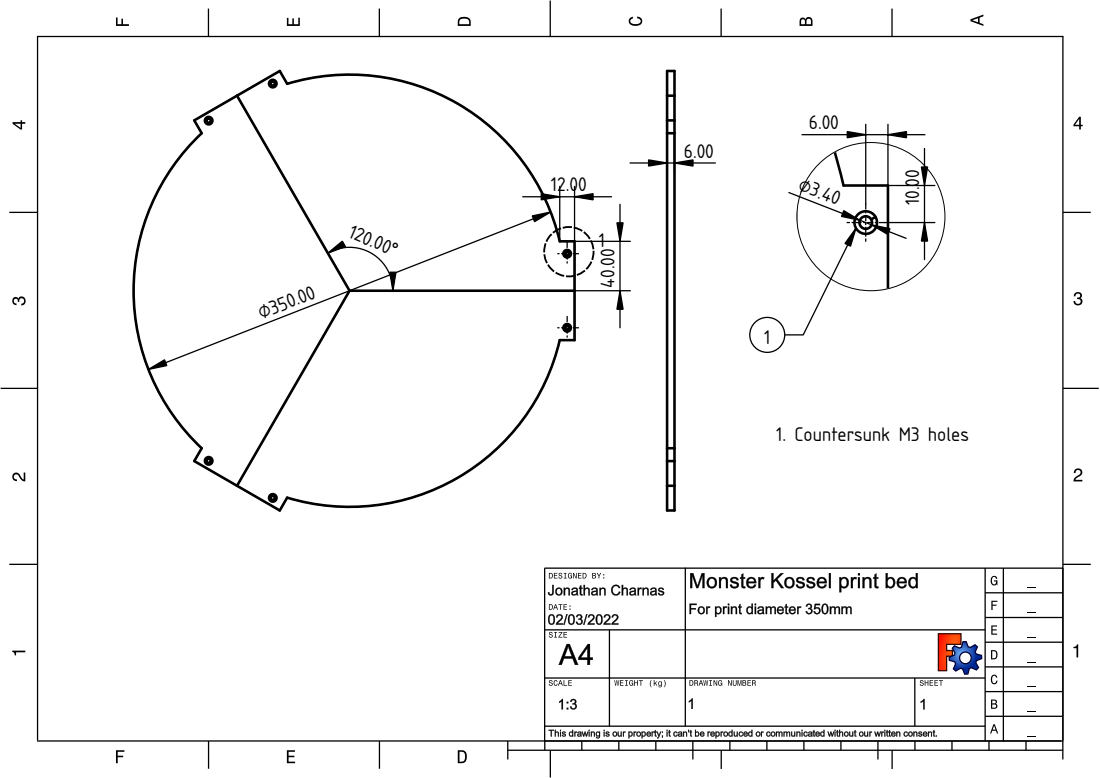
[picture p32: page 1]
⌀3.401 1. Counters; h ole

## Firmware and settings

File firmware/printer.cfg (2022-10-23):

# Generic Recore config

[recore]
revision: A6
gain_t0: 1
gain_t1: 1
gain_t2: 1
gain_t3: 1
pullup_t0: 1
pullup_t1: 1
pullup_t2: 1
pullup_t3: 1
offset_t0: 0
offset_t1: 0
offset_t2: 0
offset_t3: 0

# The STM32F031 mcu
[mcu]
serial: /dev/ttyS4
baud: 250000
restart_method: command

# The AR100 mcu
[mcu ar100]
serial: /dev/ttyS1
baud: 1500000

[static_digital_output endstops_5V_enable]
pins: ar100:PF2

# pin high = 12V, pin low = 5V
[static_digital_output endstop_ES0_5V_12V]
pins: !ar100:PF0

[static_digital_output temperature_5V_enable]
pins: ar100:PF1

[static_digital_output user_led_enable]
pins: PA12

[printer]
kinematics: delta
max_velocity: 200
max_accel: 3000
max_z_velocity: 200
minimum_z_position: -5
#delta_radius: 188.74444051245343

[tmc2209 stepper_a]
uart_pin: ar100:PB1
tx_pin: ar100:PB0
uart_address: 0
run_current: 0.750
interpolate: True
stealthchop_threshold: 99999

[tmc2209 stepper_b]
uart_pin: ar100:PB1
tx_pin: ar100:PB0
uart_address: 1
run_current: 0.750
interpolate: True
stealthchop_threshold: 99999

[tmc2209 stepper_c]
uart_pin: ar100:PB1
tx_pin: ar100:PB0
uart_address: 2
run_current: 0.750
interpolate: True
stealthchop_threshold: 99999

[tmc2209 extruder]
uart_pin: ar100:PB1
tx_pin: ar100:PB0
uart_address: 3
run_current: 0.900
interpolate: True
stealthchop_threshold: 99999

[stepper_a]
step_pin: ar100:PL4
dir_pin: !ar100:PE8
endstop_pin: ar100:PH7
rotation_distance: 32
microsteps: 32
#position_endstop: 443
#arm_length: 399
homing_speed: 100.0

[stepper_b]
step_pin: ar100:PL5
dir_pin: !ar100:PE9
endstop_pin: ar100:PH8
rotation_distance: 32
microsteps: 32
#position_endstop: 441

[stepper_c]
step_pin: ar100:PL6
dir_pin: !ar100:PE10
endstop_pin: ar100:PH9
rotation_distance: 32
microsteps: 32
#position_endstop: 443

[extruder]
step_pin: ar100:PL7
dir_pin: !ar100:PE11
heater_pin: PA8
sensor_type: ATC Semitec 104GT-2 #ATC Semitec 104NT-4-R025H42G
sensor_pin: PA0
rotation_distance: 11.662 # 16 microsteps: 7.710843373493976
microsteps: 32
nozzle_diameter: 1.400
filament_diameter: 1.75
#control: pid
#pid_Kp: 22.2
#pid_Ki: 1.08
#pid_Kd: 114
min_extrude_temp: 180
max_extrude_only_distance: 150
min_temp: 0
max_temp: 300


[heater_bed]
heater_pin: PA11
sensor_type: EPCOS 100K B57560G104F
sensor_pin: PA1
#control: pid
#pid_Kp: 22.2
#pid_Ki: 1.08
#pid_Kd: 114
pwm_cycle_time: 0.2
min_temp: 10
max_temp: 100


[fan]
pin: !PB3
max_power: 0.4

[heater_fan recore_fan]
pin: PA9
heater: extruder
heater_temp: 10.0

[probe]
pin: !ar100:PH6
x_offset: 0.0
y_offset: 0.0
z_offset: -0.085
speed: 10.0
samples: 5
sample_retract_dist: 2.0
lift_speed: 100.0
samples_result: median
samples_tolerance: 0.100
samples_tolerance_retries: 2

[delta_calibrate]
radius: 120.0
speed: 50
horizontal_move_z: 5

[virtual_sdcard]
path: /usr/share/models/

#[filament_switch_sensor sentinel]
#pause_on_runout: True
#runout_gcode:
#  MY_PAUSE
#switch_pin: ^ar100:PH4

[pause_resume]

[gcode_macro pause]
rename_existing: PAUSE_BASE
gcode:
  PAUSE_BASE
  SAVE_GCODE_STATE NAME=my_move_up_state
  G91
  G1 Z10
  G90
  RESTORE_GCODE_STATE NAME=my_move_up_state

#[gcode_macro resume]
#rename_existing: RESUME_BASE
#gcode:
#  SAVE_GCODE_STATE NAME=my_move_down_state
#  G91
#  G1 Z-10
#  G90
#  RESTORE_GCODE_STATE NAME=my_move_down_state

[gcode_macro RESUME]
description: Resume the actual running print
rename_existing: RESUME_BASE
gcode:
  ##### read extrude from  _TOOLHEAD_PARK_PAUSE_CANCEL  macro #####
  {% set extrude = printer['gcode_macro _TOOLHEAD_PARK_PAUSE_CANCEL'].extrude %}
  #### get VELOCITY parameter if specified ####
  {% if 'VELOCITY' in params|upper %}
    {% set get_params = ('VELOCITY=' + params.VELOCITY)  %}
  {%else %}
    {% set get_params = "" %}
  {% endif %}
  ##### end of definitions #####
  {% if printer.extruder.can_extrude|lower == 'true' %}
    M83
    G1 E{extrude} F2100
    {% if printer.gcode_move.absolute_extrude |lower == 'true' %} M82 {% endif %}
  {% else %}
    {action_respond_info("Extruder not hot enough")}
  {% endif %}  
  RESUME_BASE {get_params}

[gcode_macro CANCEL_PRINT]
description: Cancel the actual running print
rename_existing: CANCEL_PRINT_BASE
variable_park: True
gcode:
  ## Move head and retract only if not already in the pause state and park set to true
  {% if printer.pause_resume.is_paused|lower == 'false' and park|lower == 'true'%}
    _TOOLHEAD_PARK_PAUSE_CANCEL
  {% endif %}
  TURN_OFF_HEATERS
  CANCEL_PRINT_BASE

[gcode_macro _TOOLHEAD_PARK_PAUSE_CANCEL]
description: Helper: park toolhead used in PAUSE and CANCEL_PRINT
variable_extrude: 1.0
gcode:
  ##### set park positon for x and y #####
  # default is your max posion from your printer.cfg
  {% set x_park = 0.0 %}
  {% set y_park = 0.0 %}
  {% set z_park_delta = 25.0 %}
  ##### calculate save lift position #####
  {% set max_z = printer.toolhead.axis_maximum.z|float %}
  {% set act_z = printer.toolhead.position.z|float %}
  {% if act_z < (max_z - z_park_delta) %}
    {% set z_safe = z_park_delta %}
  {% else %}
    {% set z_safe = max_z - act_z %}
  {% endif %}
  ##### end of definitions #####
  {% if printer.extruder.can_extrude|lower == 'true' %}
    M83
    G1 E-{extrude} F2100
    {% if printer.gcode_move.absolute_extrude |lower == 'true' %} M82 {% endif %}
  {% else %}
    {action_respond_info("Extruder not hot enough")}
  {% endif %}
  {% if "xyz" in printer.toolhead.homed_axes %}
    G91
    G1 Z{z_safe} F900
    G90
    G1 X{x_park} Y{y_park} F6000
    {% if printer.gcode_move.absolute_coordinates|lower == 'false' %} G91 {% endif %}
  {% else %}
    {action_respond_info("Printer not homed")}
  {% endif %}

[include mainsail.cfg]
[include timelapse.cfg]
# Set up board voltage, current, temperature.

[temperature_sensor board]
sensor_type: EPCOS 100K B57560G104F
sensor_pin: PA6
max_temp: 110
gcode_id: Board

[temperature_sensor cold_junction]
sensor_type: EPCOS 100K B57560G104F
sensor_pin: PA7
gcode_id: CJ

# Vout = Vin * 10K/110K = Vin*11
[adc_temperature v]
temperature1: 0.35
voltage1: 0
temperature2: 36.65
voltage2: 3.3

[temperature_sensor voltage]
adc_voltage: 3.3
sensor_pin: PA4
sensor_type: v
gcode_id: Voltage

# 1 A = 20 mV
[adc_temperature current]
temperature1: 0
voltage1: 0
temperature2: 165
voltage2: 3.3

[temperature_sensor current]
adc_voltage: 3.3
sensor_pin: PA5
sensor_type: current
max_temp: 20
gcode_id: Current

[gcode_button over_current_alarm]b
pin: !ar100:PF6
press_gcode: M112

#*# <---------------------- SAVE_CONFIG ---------------------->
#*# DO NOT EDIT THIS BLOCK OR BELOW. The contents are auto-generated.
#*#
#*# [printer]
#*# delta_radius = 189.582465
#*#
#*# [stepper_a]
#*# angle = 209.822175
#*# position_endstop = 447.309133
#*# arm_length = 399.000000
#*#
#*# [stepper_b]
#*# angle = 330.018110
#*# position_endstop = 444.645261
#*# arm_length = 399.000000
#*#
#*# [stepper_c]
#*# angle = 90.000000
#*# position_endstop = 443.623700
#*# arm_length = 399.000000
#*#
#*# [heater_bed]
#*# control = pid
#*# pid_kp = 43.132
#*# pid_ki = 0.836
#*# pid_kd = 556.408
#*#
#*# [extruder]
#*# control = pid
#*# pid_kp = 33.700
#*# pid_ki = 1.468
#*# pid_kd = 193.355
#*#
#*# [delta_calibrate]
#*# height0 = -0.085
#*# height0_pos = 89463.000,88956.000,88747.000
#*# height1 = -0.085
#*# height1_pos = 100161.000,99656.000,80589.000
#*# height2 = -0.085
#*# height2_pos = 86982.000,106101.000,86283.000
#*# height3 = -0.085
#*# height3_pos = 81817.000,98083.000,97856.000
#*# height4 = -0.085
#*# height4_pos = 86996.000,86488.000,100939.000
#*# height5 = -0.085
#*# height5_pos = 97090.000,81877.000,96357.000
#*# height6 = -0.085
#*# height6_pos = 104021.000,86427.000,86232.000

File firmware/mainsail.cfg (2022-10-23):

[pause_resume]

[display_status]

[virtual_sdcard]
path: /home/debian/gcode_files

[gcode_macro CANCEL_PRINT]
description: Cancel the actual running print
rename_existing: CANCEL_PRINT_BASE
variable_park: True
gcode:
  ## Move head and retract only if not already in the pause state and park set to true
  {% if printer.pause_resume.is_paused|lower == 'false' and park|lower == 'true'%}
    _TOOLHEAD_PARK_PAUSE_CANCEL
  {% endif %}
  TURN_OFF_HEATERS
  CANCEL_PRINT_BASE

[gcode_macro SET_BOOT_MEDIA_USB]
description: Switch boot media to USB. After a reboot the board is running from a USB drive.
gcode:
    { action_call_remote_method("set_boot_media", boot_media="usb") }
    { action_respond_info("Boot media set to USB. Press reboot to boot from USB.")}

[gcode_macro SET_BOOT_MEDIA_EMMC]
description: Switch boot media to EMMC. After a reboot the board is running from the eMMC drive
gcode:
    { action_call_remote_method("set_boot_media", boot_media="emmc") }
    { action_respond_info("Boot media set to eMMC. Press reboot to boot from eMMC")}

[gcode_macro SET_SSH_ACCESS_ON]
description: Enable the user to log in via ssh.
gcode:
    { action_call_remote_method("set_ssh_access", is_enabled=true) }
    { action_respond_info("SSH access is now enabled")}

[gcode_macro SET_SSH_ACCESS_OFF]
description: Enable the user to log in via ssh.
gcode:
    { action_call_remote_method("set_ssh_access", is_enabled=false) }
    { action_respond_info("SSH access is now disabled")}

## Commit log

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2020-04-17 UPDATED: hole management on bottom corner. Added M5 for 2040 lock-in.
    [Bed.FCStd, PrecisionPiezoAndromeda.FCStd, Rail_Carriage.FCStd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]
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2020-04-17 last update to top corner for the night.
    [topCorner.FCStd]
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2020-04-25 Adding materials and fixed piezo mounts after receiving PCBs for mounting
    [Bed.FCStd, OpenBeam450mm.FCStd, OpenBuilds2060.FCStd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]
2020-04-25 Changed from countersink to counterbore on 2060 M5 holes.
    [Bed.FCStd, PrecisionPiezoAndromeda.FCStd, Rail_Carriage.FCStd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]
2020-05-15 Added wiring holes in bottom frame, motor frame. Aligned rails with top corners in assembly.
    [Bed.FCStd, OpenBuilds2040.FCStd, PrecisionPiezoAndromeda.FCStd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]
2020-05-15 Update to the assembly wasn't saved after motor frame update.
    [bottomAssembly.FCStd]
2020-05-15 Added pass through holes in top corners for wires/misc things, aligned top and bottom openbeams and added slider notches for acrylic panels
    [bottomAssembly.FCStd, bottomCorner.FCStd, topCorner.FCStd]
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2020-05-24 Added side panels, fixed alignment of motor frames to the bed with offset for bed holes to line up with andromeda probe sensors.
    [Bed.FCStd, PrecisionPiezoAndromeda.FCStd, Rail_Carriage.FCStd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]
2020-05-25 Added top cover acrylic plate with opening for 100mm extraction fan (common ventilation AC fan size in EU).
    [Bed.FCStd, Nema17WithPulley.FCStd, OpenBeam450mm.FCStd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]
2020-05-25 Added A2 Plus assembly file, which was used to generate POV-Ray preview render.
    [topCorner.FCStd]
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2020-06-10 Fixed gimbal threading for 3D printing tolerances. Fixed STLs.
    [Telescopic_shaft_axle_fitting.stl, Telescopic_shaft_cap.stl, Telescopic_shaft_link.stl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]
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2020-06-17 Fixed U-joint for telescopic shaft with bearing mounts.
    [Telescopic_shaft_axle_fitting.stl, Telescopic_shaft_link.stl, telescopic_shaft_outer.FCStd]
2020-06-17 Fixed U-joint clearances for proper rotation.
    [Telescopic_shaft_cap.stl, Telescopic_shaft_link.stl, telescopic_shaft_outer.FCStd]
2020-06-19 Fixed the telescopic shaft's axle fitting with a chamfer for added strength.
    [Telescopic_shaft_axle_fitting.stl, telescopic_shaft_outer.FCStd]
2020-06-24 Finished version of the telescopic shaft parts, export of frame to STL for printing.
    [Telescopic_shaft_link.stl, bottom_corner.stl, carriage.stl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]
2020-07-03 Adding bottom to pockets to prevent warping during printing.
    [bottomCorner.FCStd, bottom_corner.stl]
2020-07-10 Redrew the rod holding carriage for an MGN9C rail package instead of MGN9H pattern.
    [carriage_MGN9C.FCStd, mgn9c_carriage.stl]
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2020-07-12 Fixed the rod end mounting position from bottom to top of the carriage.
    [carriage_MGN9C.FCStd, mgn9c_carriage.stl]
2020-07-12 Updated README and removed Assembly4-related file as it is no longer used.
    [bottomAssembly.FCStd]
2020-07-14 Fixed carriage nut pocket depths after first prints. (they were 0.5mm too deep), adjusted axle fitting nut pocket for telescopic shaft axle fitting from dimensions learned on carriages.
    [Telescopic_shaft_axle_fitting.stl, carriage_MGN9C.FCStd, mgn9c_carriage.stl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]
2020-07-15 Updated the carriage height to account for reworked V3 geometry instead of V2's.
    [carriage_MGN9C.FCStd, mgn9c_carriage.stl]
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2020-07-21 Added STEP file exports. New 4mm-axle shaft cap for using commercial U-joints.
    [Telescopic_shaft_axle_fitting.stl, bottom_corner.step, kossel_carriage_MGN9C.step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]
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2020-07-24 Added tolerance for 15x15 to bottom corner after first print & test fit.
    [bottomCorner.FCStd, bottom_corner.step, bottom_corner.stl]
2020-07-24 Added tolerance for 15x15 to top corner.
    [topCorner.FCStd, top_corner.step, top_corner.stl]
2020-08-05 Fixed Andromeda mounting pocket dimensions after motor frame prints.
    [motorFrame.FCStd, motor_frame.step, motor_frame.stl]
2020-09-20 Adding an attempt for a fan shroud using a 4020 blower fan.
    [4020fan.STEP, E3D_v6_Assembly.STEP, assembly_a2plus.FCStd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]
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2021-05-02 Assembly fixed, top cover mounting holes added
    [assembly_a2plus.FCStd, top_cover.FCStd]
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2021-10-31 Added Hiwin MGN9 STEP files for rails & carriages. \nGenerated full assembly based on top, bottom & tower assemblies for easier editing. \nFixed M5 passing hole in bottom corner (was M2 diameter befo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
    [MGN9-C v2.stl, MGN9C.FCStd, MGN9CZFC-HiwinCorporation-3D-10-31-2021.stp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]
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2021-11-04 Added tolerances for top and tower assemblies.
    [top_assembly.FCStd, tower_assembly.FCStd]
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2021-11-04 Added BOM section to the README, to be completed once assembly with all fasteners is completed.
    [top_cover.FCStd]
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2021-11-17 Restarting the main assembly after finding issues with tolerance alignments. Adding T-Nuts.
    [T NUT M5 2020S.STEP, Tee Nut.step, bottomCorner.FCStd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]
2021-11-18 Fixing constraints for bottom frame. Tower assemblies fastening with M5 screws & T-nuts completed.
    [assembly_a2plus.FCStd, bottom_frame_assembly.FCStd]
2021-11-18 Fixing the M5 screw mounting for holding onto the 2040 extrusion without blocking tightening after OpenBeam introduction.
    [topCorner.FCStd]
2021-11-18 Fixed top corner. Added OpenBeam extrusions for the top triangle.
    [assembly_a2plus.FCStd, topCorner.FCStd]
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2021-11-18 Updated STL exports of top and bottom corners as well as motor frame assembly.
    [assembly_a2plus.FCStd, bottom_corner.stl, bottom_frame_assembly.FCStd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]
2021-11-22 Completed main frame assembly. Added carriage part files and starting carriage assembly.
    [MGN9CZFC-HiwinCorporation-3D-10-31-2021.FCStd, assembly_a2plus.FCStd, carriage_assembly.FCStd]
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2021-12-15 Fixing the issues identified in #3 on the parts themselves. Assemblies to be updated.
    [4020fan.STEP, E3D_v6_Assembly.STEP, F623ZZ v2.step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]
2021-12-15 Fixing the issues identified in #3 on the parts themselves. Assemblies to be updated. (part 2)
    [bottomCorner.FCStd, bottom_frame_assembly.FCStd, motorFrame.FCStd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]
2021-12-15 Updating the BOM based on M3x10 length issue described in #3
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2021-12-23 Adding 0.2mm tolerance for 2040 and 2060 fitting in the bottom corner.
    [bottomCorner-M3x10.FCStd, bottomCorner.FCStd, bottom_corner-M3x10.step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]
2021-12-23 Fixing hole alignments for motor frame mount that was causing issues.
    [bottomCorner-M3x10.FCStd, bottom_corner-M3x10.step, bottom_corner-M3x10.stl]
2021-12-27 Added tolerances to top corner part for the 2040 and 2060 extrusions to fit.
    [topCorner.FCStd, top_corner.step, top_corner.stl]
2021-12-27 Fixed STEP export.
    [top_corner.step]
2021-12-28 Updating depth of M3 pockets on top corner for better thread grip.
    [topCorner.FCStd, top_corner.step, top_corner.stl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]
2022-01-05 Adding corners to hold the base from the outside onto the surface the printer will be affixed to.
    [Base_corner_holder.FCStd, Base_corner_holder.step, Base_corner_holder.stl]
2022-01-10 Adding optional CPAP fan & driver mounting plates. Correcting carriage thickness.
    [CPAP-fan-driver-mounting-plate-BodyPocket.step, CPAP-fan-driver-mounting-plate-BodyPocket.stl, CPAP-fan-driver-mounting-plate.FCStd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]
2022-01-13 Fixing belt passage groove in the carriage.
    [carriage_MGN9C.FCStd, kossel_carriage_MGN9C.step, mgn9c_carriage.stl]
2022-01-14 Widening the belt trench even further on the carriage, to avoid any kind of friction occurring.
    [carriage_MGN9C.FCStd, kossel_carriage_MGN9C.step, mgn9c_carriage.stl]
2022-01-14 Adding filets to outside edges and cable passages, to be more human and cable friendly.
    [bottomCorner-M3x10.FCStd, bottomCorner.FCStd, bottom_corner-M3x10.step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]
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2022-02-07 Attaching carriages, having issues with constraints.
    [MonsterKossel_assembly.FCStd, carriage_MGN9C.FCStd]
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2022-02-14 Updated top corner with Nema mounting holes to address #6. Created subassemblies for Assembly3 plugin to address #4 (incomplete).
    [CPAP_box_base.step, CPAP_box_base.stl, CPAP_box_cover.step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]
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2022-02-15 Fixed Piezo and motor frame assemblies.
    [Bed.FCStd, Nema17WithPulley.FCStd, PrecisionPiezoAndromeda.FCStd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]
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2022-02-23 Added multiple improvements and subassemblies. Added wiring diagram in documentation. Printable M12 nut for holding the heatsink to the effector.
    [Bed.FCStd, M12_printable_nut.FCStd, M12_printable_nut.step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]
2022-03-06 Fixed assemblies, created drawing for printbed manufacture.
    [Bed-6mm.step, Bed.FCStd, M12_printable_nut.step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]
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2022-03-06 Fixing top cover part dimensions after redrawing of top corner pieces.
    [MonsterKossel_assembly.FCStd, topCorner.FCStd, top_corner_assembly.FCStd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]
2022-03-11 Fixing assemblies up to the chassis.
    [Bed.FCStd, MGN9C.FCStd, MGN9CZFC-HiwinCorporation-3D-10-31-2021.FCStd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]
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2022-03-12 Fixing the bed shape sketch visibility.
    [Bed.FCStd]
2022-03-14 Fixed delta motion assembly, added drawing to compute max angle with variable rod length.
    [Assembly.FCStd, Bed.FCStd, MonsterKossel_chassis.FCStd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]
2022-03-14 Added extra screenshots to the Readme. Assemblies are completed for the mechanical parts, panels still not shown.
    [Assembly.FCStd, MonsterKossel_chassis.FCStd, Nema17WithPulley.FCStd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]
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2022-03-14 Adding missing images for optional watercooling kit brackets.
    [Base_corner_holder.FCStd]
2022-03-15 Added the complete printer assembly with panels on top of the motion assembly. Resized panels to match the resized dimensions of the pritner.
    [Assembly.FCStd, Complete_printer.FCStd, MonsterKossel_chassis.FCStd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]
2022-03-24 Updated telescoping shaft drawing with bigger tubes, using the dimensions spreadsheet and each segment having an assembly.
    [6T_Bevel_vertical_lock.stl, Bed-350mm-diameter.dxf, Complete_printer.FCStd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]
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2022-03-31 Fixed the preview.png with antialiasing.
    [Assembly.FCStd, Nema17WithPulley.FCStd, OpenBuilds2040.FCStd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]
2022-04-01 Fixed tolerances on the U-joint bearing fittings. Recomputed assembly.
    [Assembly.FCStd, Vertical_extrusion_assembly.FCStd, bearing_ujoint.FCStd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]
2022-04-02 Updated the U-joint parts for proper fit and clearances during rotation.
    [bearing_ujoint.FCStd, bearing_ujoint_cube.step, bearing_ujoint_cube.stl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]
2022-05-05 Partial fix for Linkstage 3 stable 2022.430
    [Assembly.FCStd, Bed.FCStd, MGN9C.FCStd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]
2022-05-06 Add intermediate rework of major assembly for latest Linkstage 3 stable version of FreeCAD.
    [Assembly.FCStd, Bed.FCStd, Delta_Effector.stl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]
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2022-05-09 Added a modified effector part that uses nuts to retain the delta rods.
    [delta-effector-nuts.step, delta-effector-nuts.stl, delta-effector.FCStd]
2022-05-09 Re-generated mirror steps in all drawn parts with the refine function to avoid having seams.
    [Assembly.FCStd, Bed.FCStd, MonsterKossel_chassis.FCStd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]
2022-05-09 Fixed bottomcorner_assembly and motor_frame_assembly after redrawing the parts.
    [bottomCorner_assembly.FCStd, motor_frame_assembly.FCStd]
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2022-05-11 Fixed all assemblies after update of Linkstage3
    [Assembly.FCStd, Bed.FCStd, MonsterKossel_chassis.FCStd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]
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2022-06-10 Added step file for cutting the insulation layer on CNC or laser cutter
    [Insulation_layer.step]
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2022-07-01 Reloaded files to work with Assembly3 WB in FreeCAD 0.20 without needing linkstage3 branch.
    [Bed.FCStd, MGN9CZFC-HiwinCorporation-3D-10-31-2021.FCStd, MGNR9R900CM-HiwinCorporation-3D-10-31-2021.FCStd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]
2022-07-01 Updated the openbuilds files to use Multitransform instead of multiple mirror steps.
    [Assembly-for-render.FCStd, MonsterKossel_chassis.FCStd, OpenBuilds2040.FCStd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]
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2022-07-11 Fixed openbuilds and vertical assembly.
    [OpenBuilds2040.FCStd, Vertical_extrusion_assembly.FCStd]
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2022-07-12 Added firmware config for Recore, and new pads for the telescoping shaft. Shaft assembly file still WIP.
    [printer.cfg, slip_pad.step, slip_pad.stl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]
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2022-08-22 Added PrusaSlicer config bundles for PLA & Flex, modified U-Joints for 4x2x2mm bearings with 2mm pins
    [Assembly-for-render.FCStd, MonsterKossel_chassis.FCStd, OpenBeam1515.FCStd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]
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2022-11-01 Fixing andromeda pocket tolerances, to get better responsiveness.
    [motorFrame.FCStd]
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
